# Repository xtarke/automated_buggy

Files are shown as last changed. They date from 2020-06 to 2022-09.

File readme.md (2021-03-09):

# Buggy AWD

Baseado em [Projeto PI3](https://github.com/luscasos/PI3-carro) de __Lucas Odair Silva.__

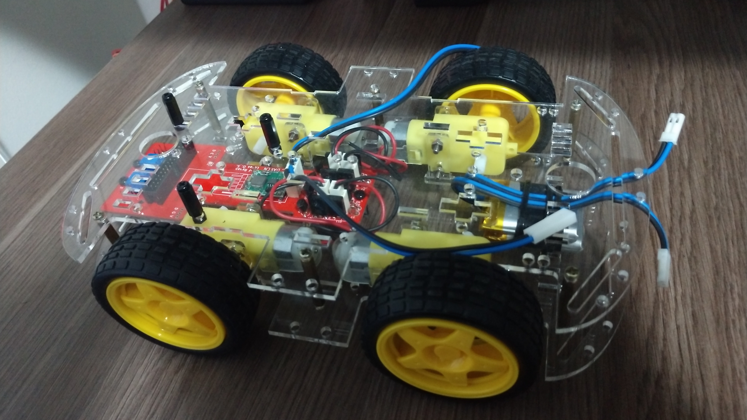
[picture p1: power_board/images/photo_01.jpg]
carro final


## Informações gerais

Projeto da placa eletrônica de potência para o acionamento de um Buggy 4x4. Um conector de 26-vias faz a conexão das seguintes placas:

- [Arduino Uno](./arduino/shield/)
- [MSP-EXP430G2](./msp430/shield_exp430g2)
- [MSP-EXP430FR2355](./msp430/shield_exp430fr2355)
- [Raspberry Pi](./rasp/)

## Características

- Controle independente dos motores (lado esquerdo e lado direito)
- Sensores de velocidade [Encoder](https://www.filipeflop.com/produto/sensor-de-velocidade-encoder/)
- Monitoramento de bateria de LiPo
- Sensor de linha dual
- Sensor ultrassom
- Comunicação Bluetooth (UART)

# Hardware

## Acionamento dos motores

Ponte H

Circuito final de alimentação dos motores, com queda de 0,4V de tensão na carga em relação a VCC e corrente de polarização externa de 640pA, não exigindo muita corrente do microcontrolador.
Ponte H

## Comunicação

HC-05

## Aferição de velocidade

encoder

## Baterias
Para alimentar o carro foram escolhidas duas baterias de LIPO, de 3,7V e 1200mAh, conectadas em série, o que resulta em 7,4V de tensão.

Bateria

## Regulador de tensão
Como o conjunto de baterias tem como tensão 7,4V na saída, é necessário baixar a tensão para níveis aceitáveis para o microcontrolador e modulo bluetooth, no caso foi usado um regulador ajustável Step-up-down, por questão de disponibilidade, mesmo esse sendo superdimensionado para a aplicação em questão, já que suporta correntes de até 5A e nesse caso não passa de 200mA.

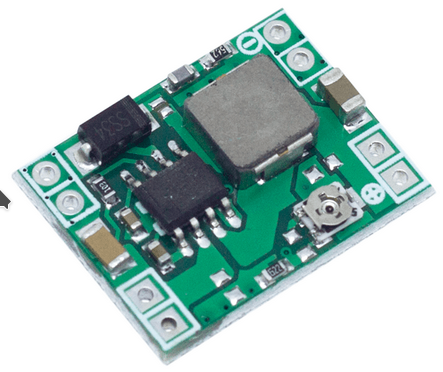
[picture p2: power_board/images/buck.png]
Regulador


## Medição da tensão das baterias
Como regra geral, não se pode descarregar uma bateria abaixo de uma certa tensão, com as usadas nesse projeto não é diferente, não sendo recomendado baixar a tensão da marca dos 3V, como o sistema possui duas baterias é necessário medir a tensão delas individualmente. O conversor analógico digital do microcontrolador tem como tensão base 3V, então é preciso baixar as tensões para menos de 3V, o circuito usado para isso é o diferencial com ampop, que pode dar um ganho menor que 1, sem usar tensão negativa. O Ampop escolhido foi o LM324, com ganho de 1/3 para a tensão superior (bateria 1 em serie com a bateria 2), e de 2/3 para a tensão media (bateria 1).
diferencial

## Placa de circuito

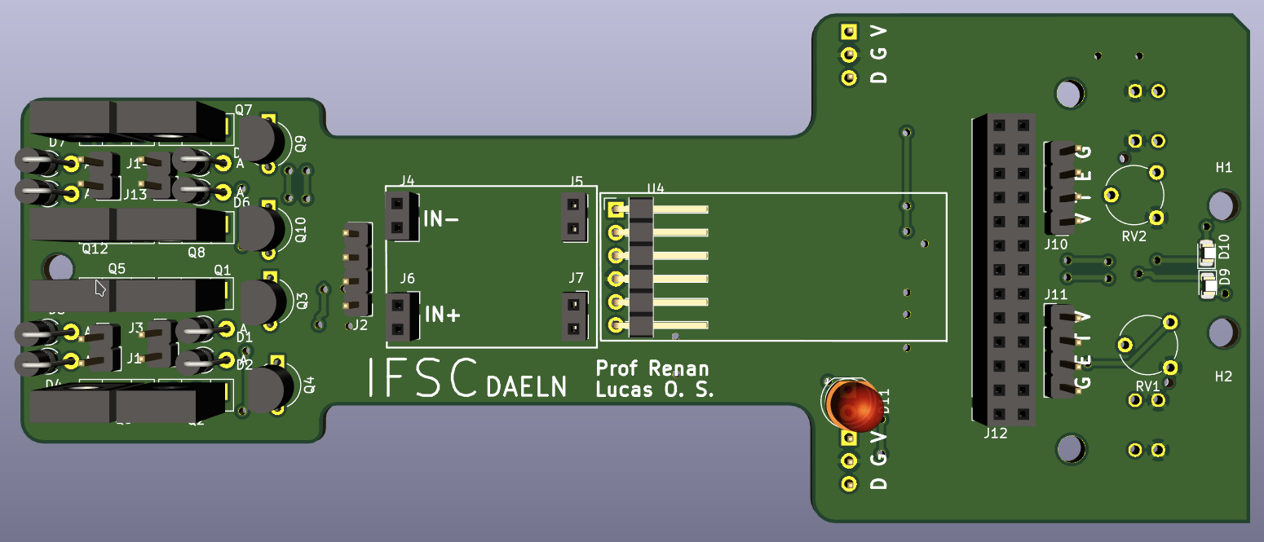
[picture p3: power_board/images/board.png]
carro visto de cima


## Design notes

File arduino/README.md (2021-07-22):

# Interface shield

This shield connects Arduino Uno pins to the car's power board. Go to [Power Board](hhttps://github.com/xtarke/automated_buggy/tree/master/power_board) for more hardware information.

See [this schematic](schematic.pdf).

## Analog pins

| Analog input  | Arduino pin  | Board label  | Signal |
| --- | --- | --- | --- |
| ADC0 | A2 | ADC0 | Bat0 |
| ADC1 | A1 | ADC1 | Bat1 |
| ADC2 | A0 | ADC2 | Ampop1 |
| ADC3 | A3 | ADC3 | Ampop2 |

## Ultrasonic sensor

| Arduino Pin | Signal|
| --- | ---|
| 8 | Echo0 |
| 7 | Trig0 |
| 2 | Echo1 |
| 4 | Trig1 |

## Motors

|Arduino Pin | Signal|  Board label |
| --- | ---| --- |
| 6 | PWM1  |  M1 |
| 5 | PWM1N |  M1N |
| 11 | PWM2  |  M2 |
| 3 | PWM2N |  M2N |

## Speed econder

| Arduino Pin | Signal |  Board label |
| --- | --- | --- |
| 13 | D0 | ENC0 |
| 12 | D1 | ENC1 |

## Optic sensor

| Arduino Pin | Signal | Board label |
| --- | --- | --- |
| A4 | R_TCRT | R DIR |
| A5 | L_TCRT | L ESQ |

## UART

| MSP Pin | Signal |
| --- | --- |
| TX | TX |
| RX | RX |

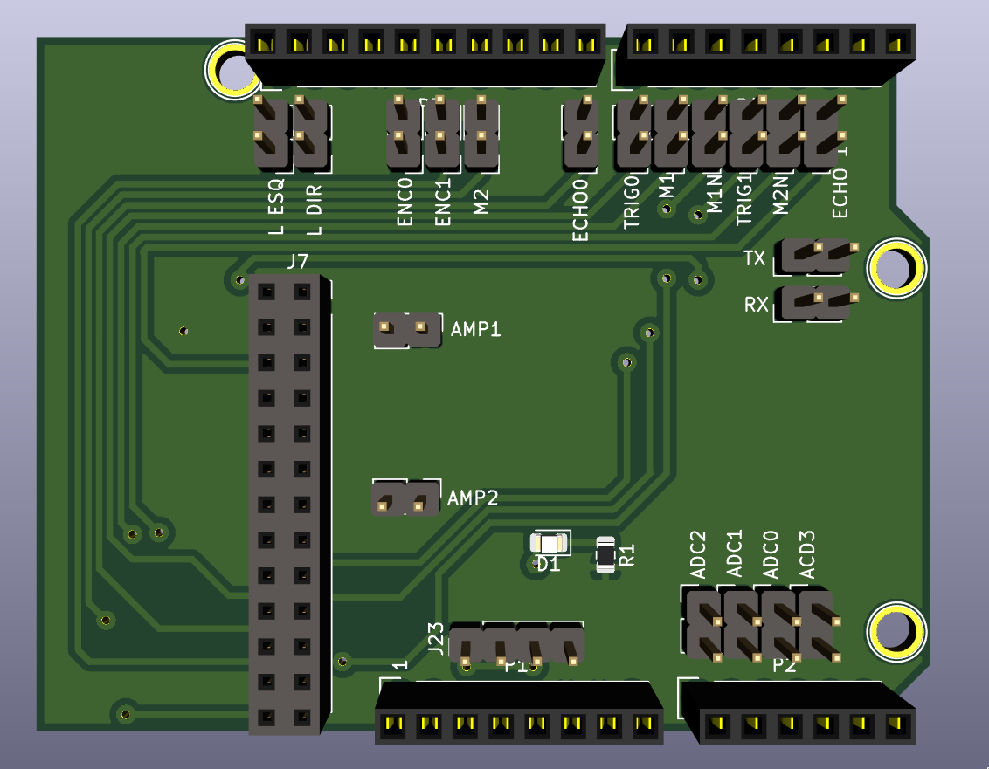
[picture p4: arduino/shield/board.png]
Board


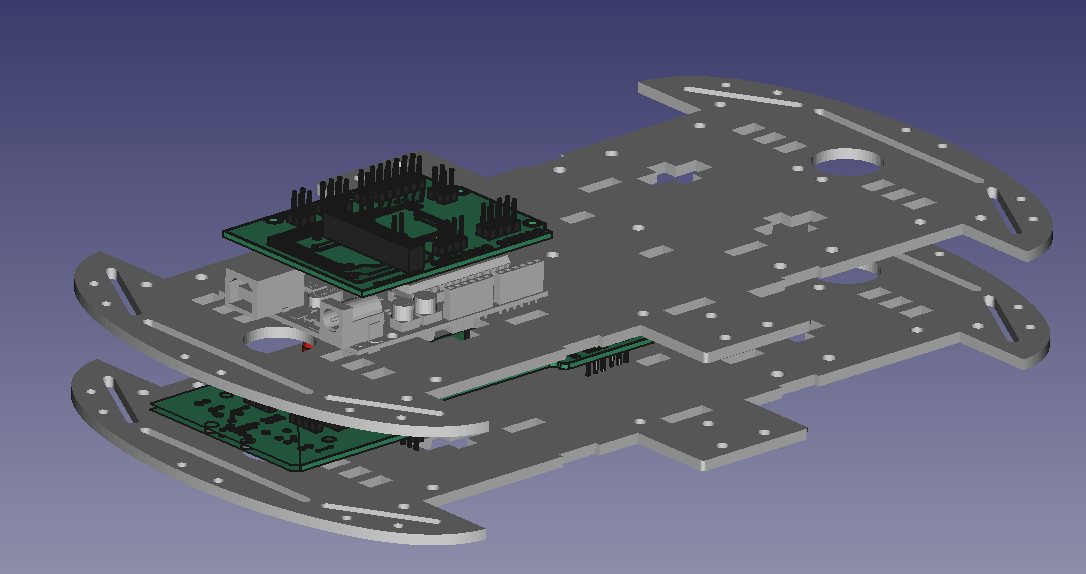
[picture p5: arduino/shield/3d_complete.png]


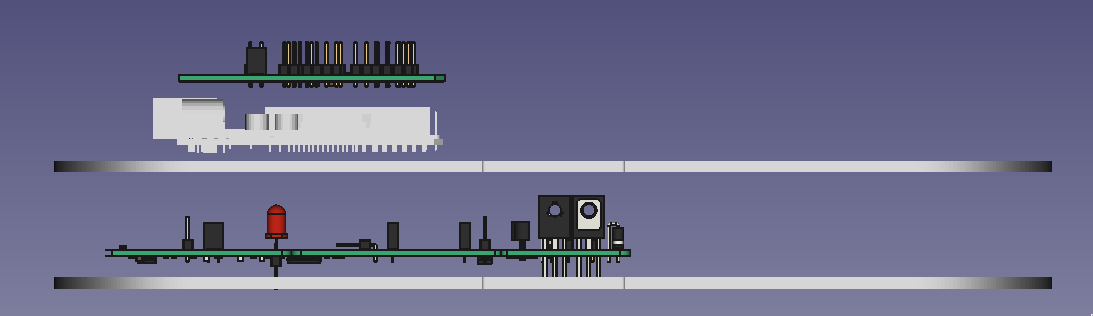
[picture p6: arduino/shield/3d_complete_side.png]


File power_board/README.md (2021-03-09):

# Placa de potência para Buggy AWD

Baseado em [Projeto PI3](https://github.com/luscasos/PI3-carro) de __Lucas Odair Silva.__

carro final

## Informações gerais

Projeto da placa eletrônica de potência para o acionamento de um Buggy 4x4. Um conector de 26-vias faz a conexão das seguintes placas:

- [Arduino Uno](https://github.com/xtarke/avrlibs/tree/master/shields/carrinho_shield)
- [MSP-EXP430G2](https://github.com/xtarke/msplibs/tree/master/hardware/shield_exp430g2)
- [MSP-EXP430FR2355](https://github.com/xtarke/msplibs/tree/master/hardware/shield_exp430fr2355)
- [Raspberry Pi](https://github.com/xtarke/automated_buggy)

## Características

- Controle independente dos motores (lado esquerdo e lado direito)
- Sensores de velocidade [Encoder](https://www.filipeflop.com/produto/sensor-de-velocidade-encoder/)
- Monitoramento de bateria de LiPo
- Sensor de linha dual
- Sensor ultrassom
- Comunicação Bluetooth (UART)

# Hardware

## Acionamento dos motores

Ponte H

Circuito final de alimentação dos motores, com queda de 0,4V de tensão na carga em relação a VCC e corrente de polarização externa de 640pA, não exigindo muita corrente do microcontrolador.
Ponte H

## Comunicação

HC-05

## Aferição de velocidade

encoder

## Baterias
Para alimentar o carro foram escolhidas duas baterias de LIPO, de 3,7V e 1200mAh, conectadas em série, o que resulta em 7,4V de tensão.

Bateria

## Regulador de tensão
Como o conjunto de baterias tem como tensão 7,4V na saída, é necessário baixar a tensão para níveis aceitáveis para o microcontrolador e modulo bluetooth, no caso foi usado um regulador ajustável Step-up-down, por questão de disponibilidade, mesmo esse sendo superdimensionado para a aplicação em questão, já que suporta correntes de até 5A e nesse caso não passa de 200mA.

Regulador

## Medição da tensão das baterias
Como regra geral, não se pode descarregar uma bateria abaixo de uma certa tensão, com as usadas nesse projeto não é diferente, não sendo recomendado baixar a tensão da marca dos 3V, como o sistema possui duas baterias é necessário medir a tensão delas individualmente. O conversor analógico digital do microcontrolador tem como tensão base 3V, então é preciso baixar as tensões para menos de 3V, o circuito usado para isso é o diferencial com ampop, que pode dar um ganho menor que 1, sem usar tensão negativa. O Ampop escolhido foi o LM324, com ganho de 1/3 para a tensão superior (bateria 1 em serie com a bateria 2), e de 2/3 para a tensão media (bateria 1).
diferencial

## Placa de circuito

carro visto de cima

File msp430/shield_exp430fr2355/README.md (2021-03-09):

# Interface shield

This shield connects microcontroller (MSP-EXP430FR2355) pins to the car's power board. Go to [Power Board](https://github.com/xtarke/automated_buggy/tree/master/power_board) for more hardware information.

See [this schematic](schematic.pdf).

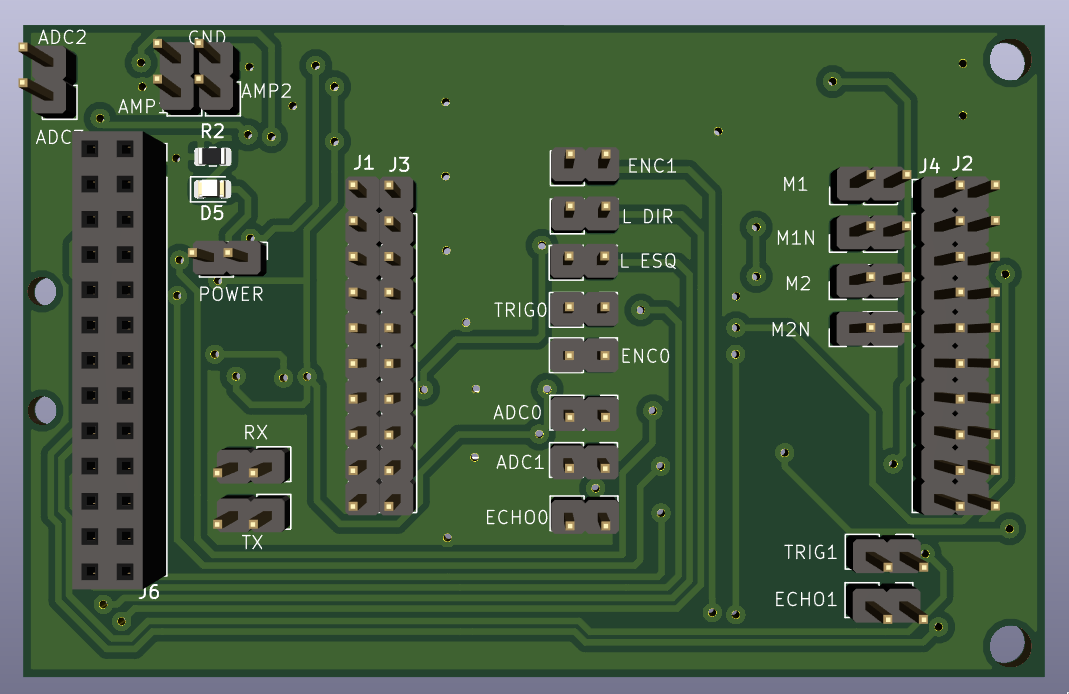
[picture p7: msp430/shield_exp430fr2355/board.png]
Board


## Analog pins

| Analog input  | MSP pin  | Board label  | Signal |
| --- | --- | --- | --- |
| A1 | P1.1 | ADC0 | Bat0 |
| A2 | P1.2 | ADC1 | Bat1 |
| ? |  ? | ADC2 | Ampop1 |
| ? |  ? | ADC3 | Ampop2 |

## Ultrasonic sensor

| MSP Pin | Signal|
| --- | ---|
| P2.0/TB1.1  | Echo0 |
| P2.2 | Trig0 |
| P2.1/TB1.2  | Echo1 |
| P2.4 | Trig1 |

## Motors

| MSP Pin | Signal|  Board label |
| --- | ---| --- |
| P6.0/TB3.1 | PWM1  |  M1 |
| P6.1/TB3.2 | PWM1N |  M1N |
| P6.2/TB3.3 | PWM2  |  M2 |
| P6.3/TB3.4 | PWM2N |  M2N |

## Espeed econder

| MSP Pin | Signal |  Board label |
| --- | --- | --- |
| P5.0 | D0 | ENC0 |
| P5.1 | D1 | ENC1 |

## Optic sensor

| MSP Pin | Signal | Board label |
| --- | --- | --- |
| P5.4 | R_TCRT | R DIR |
| P3.0 | L_TCRT | L ESQ |

## UART

| MSP Pin | Signal |
| --- | --- |
| P1.7 | TX |
| P1.6 | RX |

## Assembly

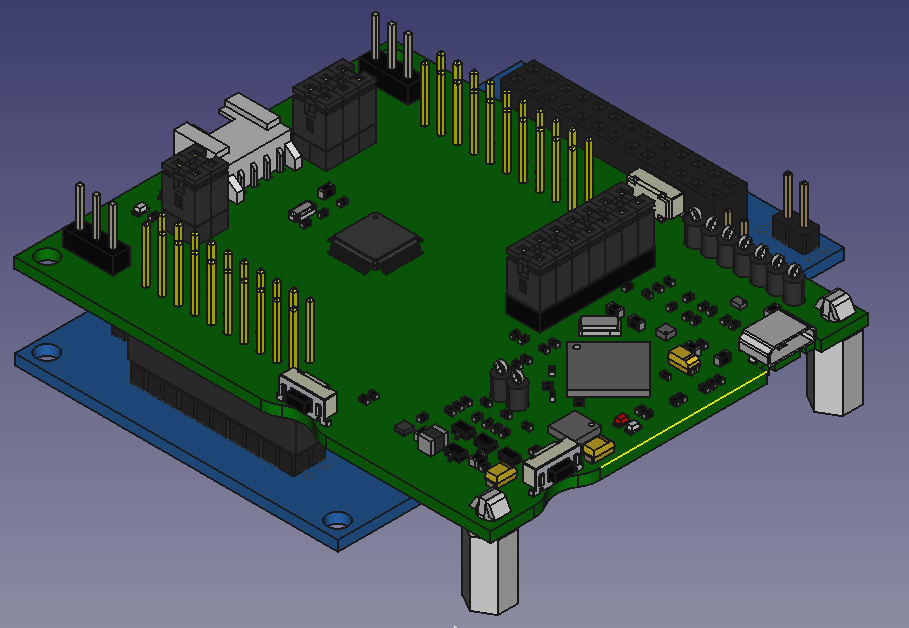
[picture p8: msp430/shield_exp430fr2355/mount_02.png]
Shield Board
Shield and EXP430FR2355 

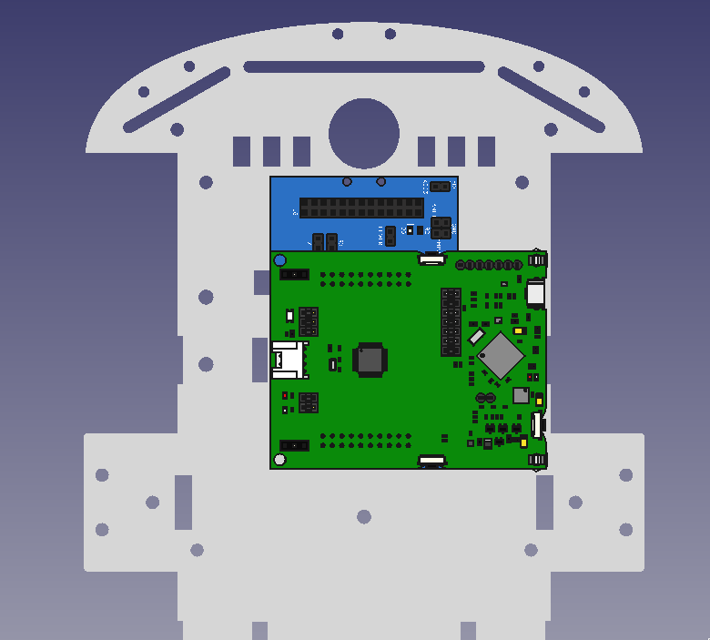
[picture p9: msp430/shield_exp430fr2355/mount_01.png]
Shield Board
Shield, EXP430FR2355 and chassi. 

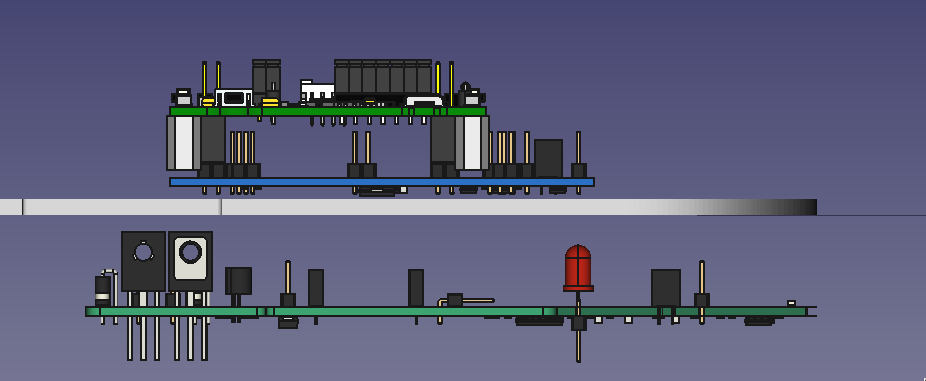
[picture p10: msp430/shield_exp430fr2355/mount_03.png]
Shield Board
Power board. Connection with 26 pin flat cable

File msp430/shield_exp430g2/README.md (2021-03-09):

# Interface shield

This shield connects all microcontroller (MSP-EXP430G2 - MSP430G2553) pins to the car's power board. Go to [Power Board](https://github.com/xtarke/automated_buggy/tree/master/power_board) for more hardware information.

See [this schematic](schematic.pdf).

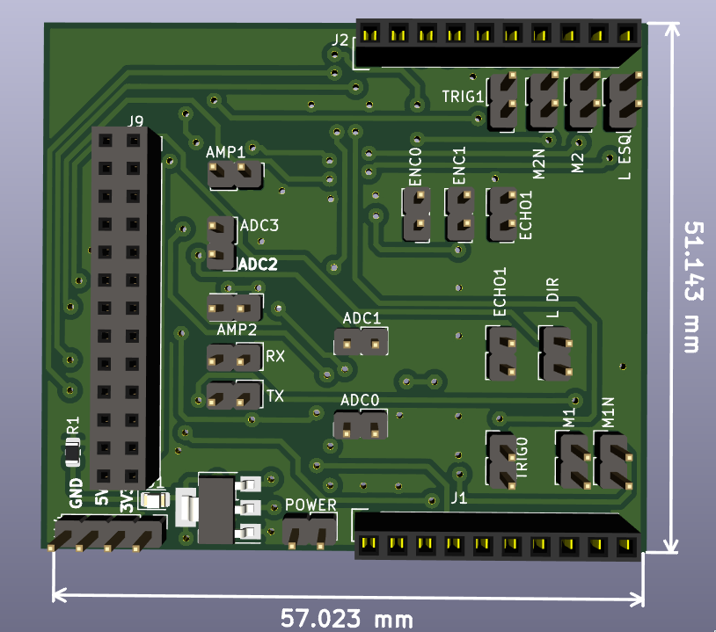
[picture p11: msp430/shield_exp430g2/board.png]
Shield Board


## Analog pins

| Analog input  | MSP pin  | Board label  | Signal |
| --- | --- | --- | --- |
| A0 | P1.0 | ADC0 | Bat0 |
| A3 | P1.3 | ADC1 | Bat1 |
| ? |  ? | ADC2 | Ampop1 |
| ? |  ? | ADC3 | Ampop2 |

## Ultrasonic sensor

| MSP Pin | Signal|
| --- | ---|
| P1.5 | Echo0 |
| P1.4 | Trig0 |
| P1.6 | Echo1 |
| P1.7 | Trig1 |

## Motors

**Caution**, P2.1 and P2.2 are connected to the same timer comparator as well as P2.4 and P2.5.

| MSP Pin | Signal|  Board label |
| --- | ---| --- |
| P2.1/TA1.1 | PWM1  |  M1 |
| P2.2/TA1.1 | PWM1N |  M1N |
| P2.4/TA1.2 | PWM2  |  M2 |
| P2.5/TA1.2 | PWM2N |  M2N |

## Espeed econder

| MSP Pin | Signal |  Board label |
| --- | --- | --- |
| P2.6 | D0 | ENC0 |
| P2.7 | D1 | ENC1 |

## Optic sensor

| MSP Pin | Signal | Board label |
| --- | --- | --- |
| P2.0 | R_TCRT | R DIR |
| P2.3 | L_TCRT | L ESQ |

## UART

| MSP Pin | Signal |
| --- | --- |
| P1.2 | TX |
| P1.3 | RX |

## Assembly

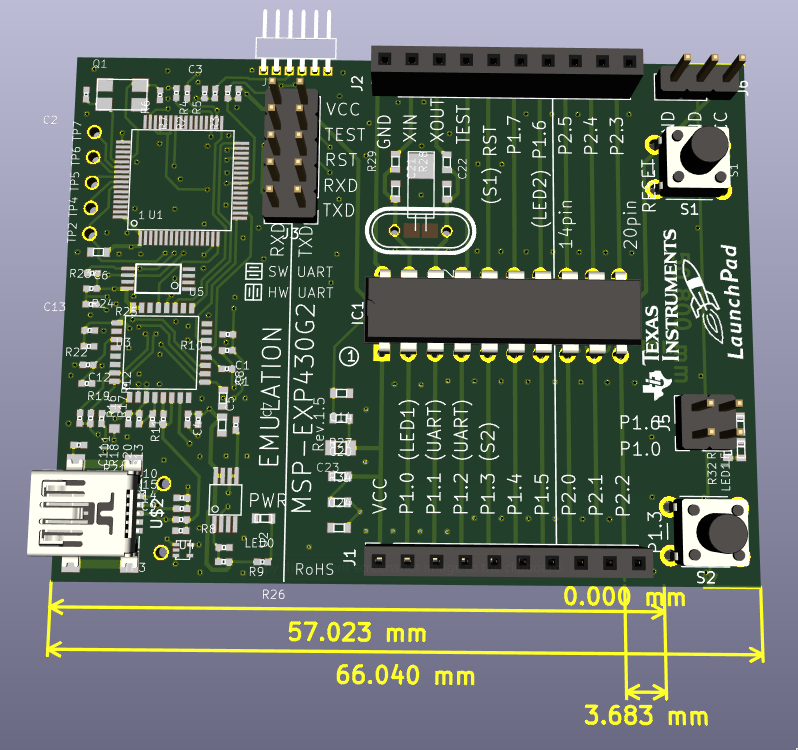
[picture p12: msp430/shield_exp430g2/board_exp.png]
Shield Board
EXP430G2 with MSP430G2553 
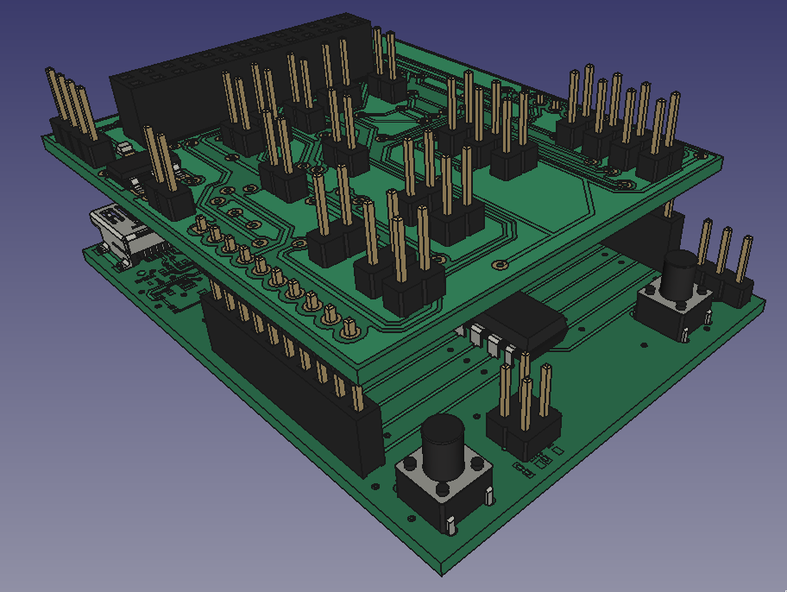
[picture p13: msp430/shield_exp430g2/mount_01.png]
Shield Board
Shield and EXP430G2 
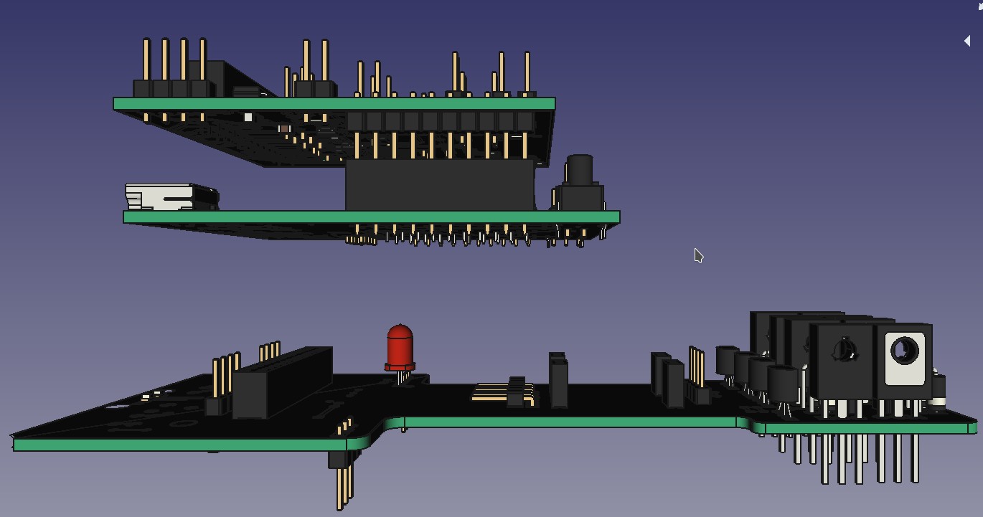
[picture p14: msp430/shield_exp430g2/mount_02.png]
Shield Board
Power board. Connection with 26 pin flat cable

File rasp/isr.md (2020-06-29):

https://raspi.tv/2013/how-to-use-interrupts-with-python-on-the-raspberry-pi-and-rpi-gpio-part-3

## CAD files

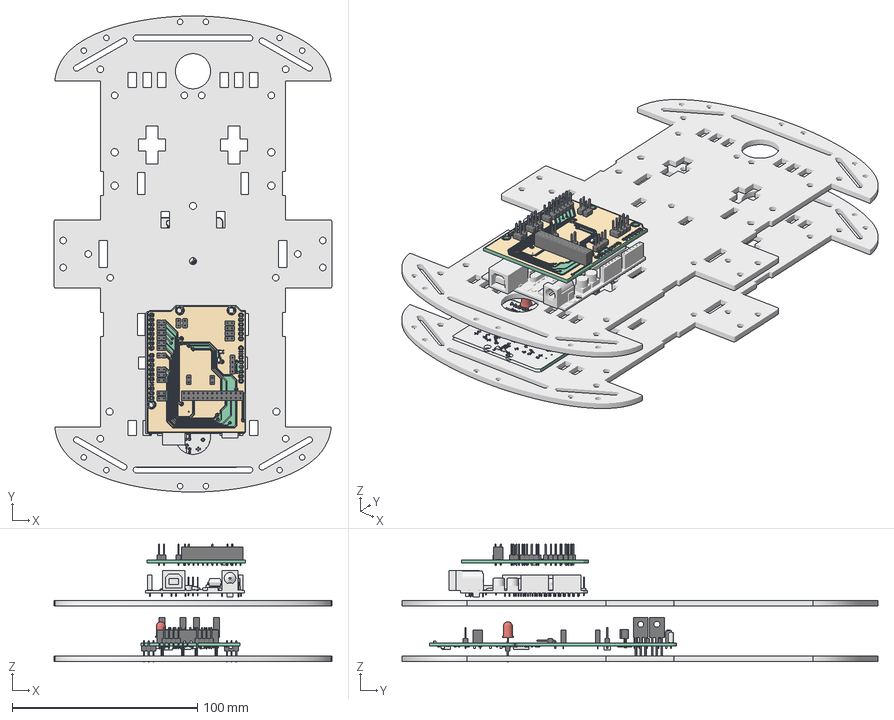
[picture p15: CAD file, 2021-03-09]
arduino/shield/3d/3dmodel.FCStd
150.0 x 257.0 x 63.7 mm
Pcb_504c
topTracks_504c
botTracks_504c
D10_LED_0805_2012Metric_5D8FAA55
D9_LED_0805_2012Metric_5D8F5CB8
Q10_TO-92_Inline_Wide_5D144232
Q4_TO-92_Inline_Wide_5D14421F
Q9_TO-92_Inline_Wide_5D14420C
Q3_TO-92_Inline_Wide_5D1441F9
J10_PinHeader_1x04_P254mm_Vertical_5CCA68DD
U4_PinHeader_1x06_P254mm_Horizontal_5D1180CB
J11_PinHeader_1x04_P254mm_Vertical_5CCA68C5
J5_PinSocket_1x02_P254mm_Vertical_5CEE14AB
J12_PinSocket_2x13_P254mm_Vertical_5CEE7202
J6_PinSocket_1x02_P254mm_Vertical_5CEE1496
J7_PinSocket_1x02_P254mm_Vertical_5CEE1481
J4_PinSocket_1x02_P254mm_Vertical_5CEE14C0
Q12_TO-126-3_Vertical_5CBBB90E
Q6_TO-126-3_Vertical_5CB9F0CD
Q8_TO-126-3_Vertical_5CB9F14F
D6_D_A-405_P2.54mm_Vertical_AnodeUp_5CC2F82E
D7_D_A-405_P2.54mm_Vertical_AnodeUp_5CC2FCEA
D2_D_A-405_P2.54mm_Vertical_AnodeUp_5CC2F84C
D3_D_A-405_P2.54mm_Vertical_AnodeUp_5D89E26B
D8_D_A-405_P2.54mm_Vertical_AnodeUp_5D84EFBF
D4_D_A-405_P2.54mm_Vertical_AnodeUp_5CC2F86A
Q1_TO-126-3_Vertical_5CBBB9BD
Q2_TO-126-3_Vertical_5CBBB9A4
Q11_TO-126-3_Vertical_5CBBB927
Q7_TO-126-3_Vertical_5CB9F135
Q5_TO-126-3_Vertical_5CB9F0E7
D1_D_A-405_P2.54mm_Vertical_AnodeUp_5CC2F85B
D5_D_A-405_P2.54mm_Vertical_AnodeUp_5CC2F800
J2_PinHeader_1x04_P254mm_Vertical_5D8375DE
J13_PinHeader_1x02_P254mm_Vertical_5D84BA2C
J14_PinHeader_1x02_P254mm_Vertical_5D84CC03
J1_PinHeader_1x02_P254mm_Vertical_5D84C8B4
J3_PinHeader_1x02_P254mm_Vertical_5D84C8C9
D11_LED_D5.0mm_5DC05149
C3_C_0805_2012Metric_5D605FC9
D12_D_SMB_5D89B82C
R35_R_0805_2012Metric_5D8A9567
U3_SOIC_14_39x87mm_P127mm_5D51740A
R34_R_0805_2012Metric_5D4B9DB6
R33_R_0805_2012Metric_5D4B9DA5
J8_PinHeader_1x03_P254mm_Vertical_5CC7F0D8
R26_R_0805_2012Metric_5D1A85D7
R25_R_0805_2012Metric_5CD50FA7
R28_R_0805_2012Metric_5CD50FDA
R31_R_0805_2012Metric_5D143DC4
C2_C_0805_2012Metric_5D1448C2
C1_C_0805_2012Metric_5D1448B1
R32_R_0805_2012Metric_5D143DB3
R12_R_0805_2012Metric_5CC39C34
R13_R_0805_2012Metric_5CC39C24
R14_R_0805_2012Metric_5CC39C14
R18_R_0805_2012Metric_5CD46DAC
R19_R_0805_2012Metric_5CD46D9B
R15_R_0805_2012Metric_5CC39C04
U1_SOIC_8_39x49mm_P127mm_5CD4E5C4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

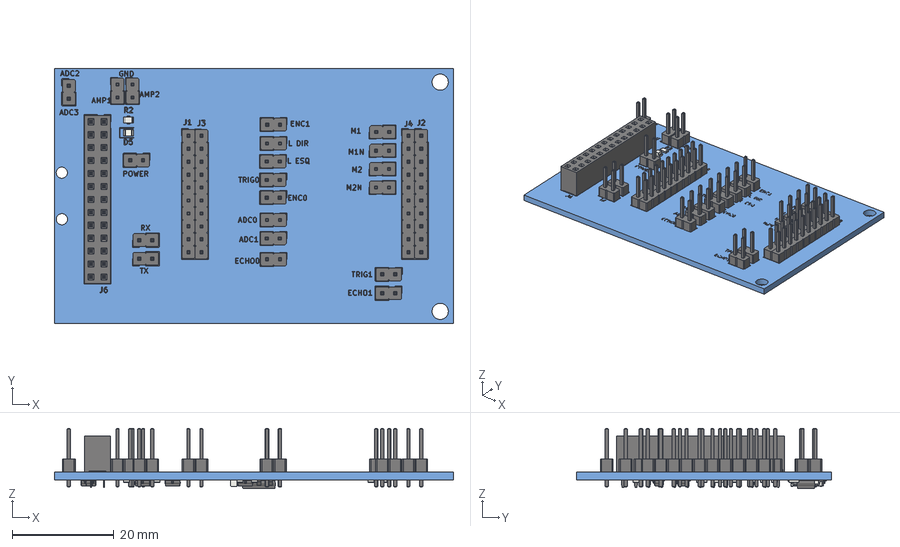
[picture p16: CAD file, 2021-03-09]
msp430/shield_exp430fr2355/3d/shield.FCStd
78.4 x 50.0 x 11.8 mm
Pcb_6e80
topSilks_5e37
J4_PinHeader_1x10_P254mm_Vertical_5EF7C818
J2_PinHeader_1x10_P254mm_Vertical_5EF7DC5C
J19_PinHeader_1x02_P254mm_Vertical_5EF86645
J28_PinHeader_1x02_P254mm_Vertical_5EF8662F
J27_PinHeader_1x02_P254mm_Vertical_5EF86619
J25_PinHeader_1x02_P254mm_Vertical_5EF88DF8
J23_PinHeader_1x02_P254mm_Vertical_5EFAA149
J7_PinHeader_1x02_P254mm_Vertical_5EF865D7
J8_PinHeader_1x02_P254mm_Vertical_5EF865C1
J9_PinHeader_1x02_P254mm_Vertical_5EF865AB
J10_PinHeader_1x02_P254mm_Vertical_5EF86595
J12_PinHeader_1x02_P254mm_Vertical_5EF8E749
J13_PinHeader_1x02_P254mm_Vertical_5EF86569
J15_PinHeader_1x02_P254mm_Vertical_5EF86553
J16_PinHeader_1x02_P254mm_Vertical_5EF9213C
J17_PinHeader_1x02_P254mm_Vertical_5EF86527
J18_PinHeader_1x02_P254mm_Vertical_5EF919EE
J20_PinHeader_1x02_P254mm_Vertical_5EF864FB
J21_PinHeader_1x02_P254mm_Vertical_5EF864E5
J22_PinHeader_1x02_P254mm_Vertical_5EF864CF
J24_PinHeader_1x02_P254mm_Vertical_5EF864B9
J14_PinHeader_1x02_P254mm_Vertical_5EF864A3
J3_PinHeader_1x10_P254mm_Vertical_5EF7D2E3
J6_PinSocket_2x13_P254mm_Vertical_5EF552A6
D5_LED_0805_2012Metric_5EF17365
R2_R_0805_2012Metric_5EF53075
J1_PinHeader_1x10_P254mm_Vertical_5EF7B795
C2_C_0805_2012Metric_5EF37C61
C1_C_0805_2012Metric_5EF17607
U1_SOT_223_5EF17352
Q1_SOT_23_5EF1733C
D1_SOT_23_5EF17327
D2_SOT_23_5EF17312
D3_SOT_23_5EF51381
D4_SOT_23_5EF172E8
Q2_SOT_23_5EF497E2
R12_R_0805_2012Metric_5EF46901
R11_R_0805_2012Metric_5EF172AD
R10_R_0805_2012Metric_5EF1729C
R9_R_0805_2012Metric_5EF640D5
R8_R_0805_2012Metric_5EF1727A
R7_R_0805_2012Metric_5EF17269
R6_R_0805_2012Metric_5EF17258
R13_R_0805_2012Metric_5EF3A85A
R14_R_0805_2012Metric_5EF37FD2
R15_R_0805_2012Metric_5EF3AB4A
R4_R_0805_2012Metric_5EF17214
R3_R_0805_2012Metric_5EF17203
R1_R_0805_2012Metric_5EF59A96
R5_R_0805_2012Metric_5EF171E1

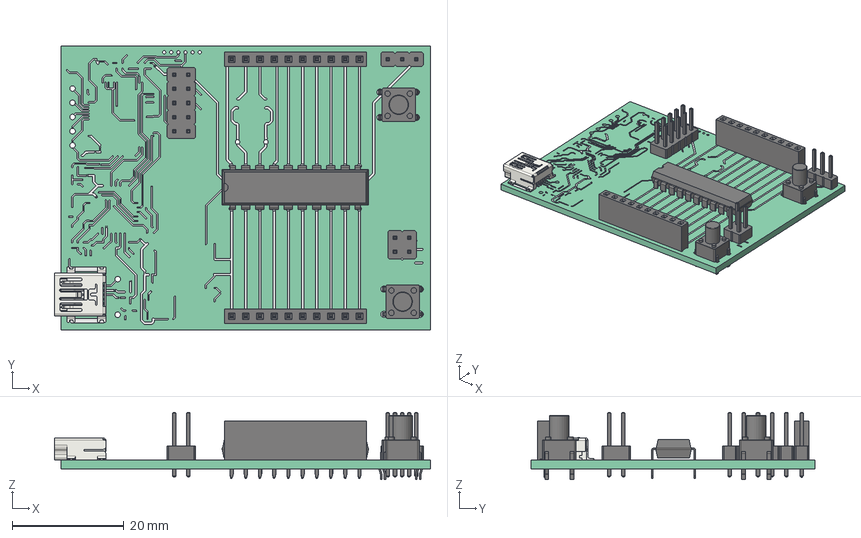
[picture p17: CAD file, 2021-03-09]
msp430/shield_exp430g2/3d/exp430g2.FCStd
67.2 x 50.8 x 12.0 mm
Pcb_a96f
topTracks_a96f
botTracks_a96f
S2_SW_PUSH_6mm_h8mm_5EF632D4
S1_SW_PUSH_6mm_h8mm_5EF632BE
U$2_USB_Mini-B_Lumberg_2486_01_Horizontal_5EF63352
J3_PinHeader_2x05_P254mm_Vertical_5EF648FA
J5_PinHeader_2x02_P254mm_Vertical_5EF648CB
J6_PinHeader_1x03_P254mm_Vertical_5EF630EB
J2_PinSocket_1x10_P254mm_Vertical_5EF6310A
J1_PinSocket_1x10_P254mm_Vertical_5EF631DF
IC1_DIP-20_W7.62mm_5EF6336D

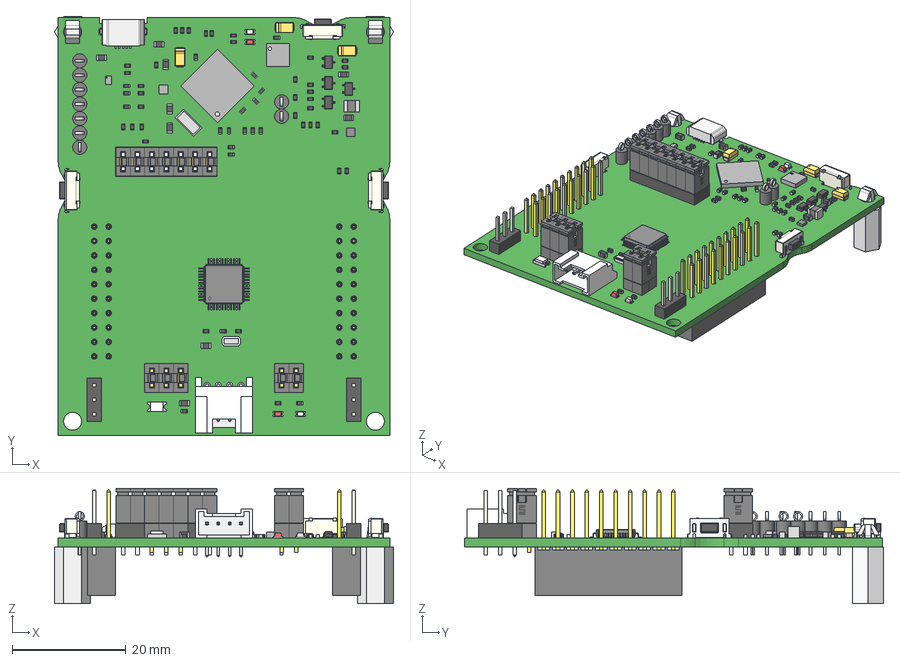
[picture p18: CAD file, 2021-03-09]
msp430/shield_exp430fr2355/3d/exp-msp430fr2355.step
59.7 x 73.9 x 20.3 mm
SamtecTSWpin x 10
SamtecTSWbody x 10
MAE-10 x 2
Extruded x 241
1188E-1K2-V-TR_1 x 3
1188E-1K2-V-TR_2 x 3
1188E-1K2-V-TR_3 x 3
1188E-1K2-V-TR_4 x 3
1188E-1K2-V-TR_5 x 3
1188E-1K2-V-TR_6 x 3
1188E-1K2-V-TR_7 x 3
PT0048A_1
PT0048A_2 x 48
Lite-On_LTST_C190 x 2
Lite-On_LTST_C190_red x 2
SSQ-110-03-T-D_2 x 2
SSQ-110-03-T-D_1 x 2
Case_Anode_2 x 3
Case_Bottom_2 x 3
Case_Cathode_2 x 3
Case_Top_2_2 x 3
User_Library-SC-70_pin_TSSOP_tssop6_1 x 12
User_Library-SC-70_body_TSSOP-6_SC70_1 x 4
FRAME-RSE0008A_3
FRAME-RSE0008A_4
FRAME-RSE0008A_5
FRAME-RSE0008A_6
FRAME-RSE0008A_7
FRAME-RSE0008A_8
FRAME-RSE0008A_9
FRAME-RSE0008A_10
BODY-QFN
PIN1-ID
Keystone5001_black x 9
Keystone500x_wire x 9
c-37-x x 12
snt-100-xx x 12

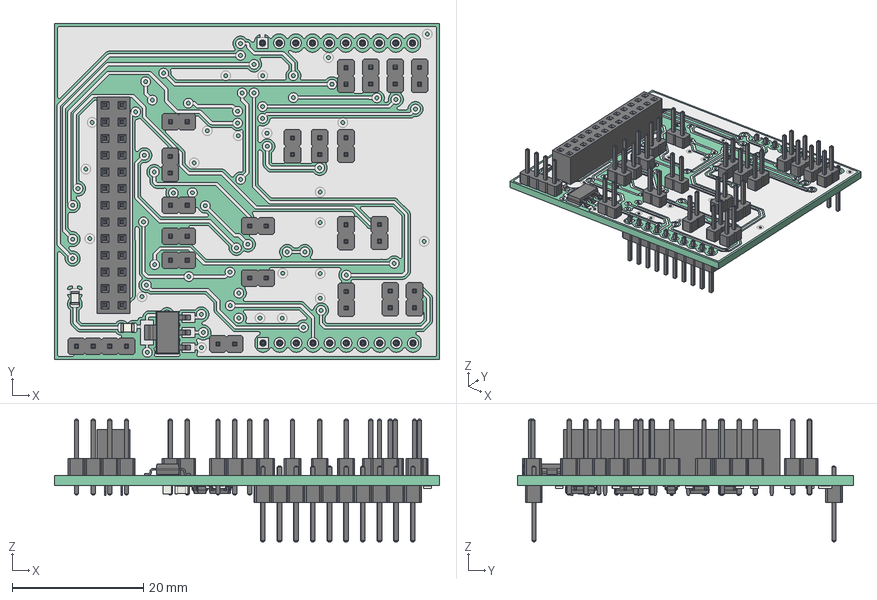
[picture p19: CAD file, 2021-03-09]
msp430/shield_exp430g2/3d/shield.FCStd
58.7 x 51.2 x 18.7 mm
Pcb_48dc
topTracks_48dc
botTracks_48dc
POWER_PinHeader_1x02_P254mm_Vertical_5EE1416E
J9_PinSocket_2x13_P254mm_Vertical_5EE14100
U1_SOT_223_5EEEE608
ADC1_PinHeader_1x02_P254mm_Vertical_5EE15095
ADC0_PinHeader_1x02_P254mm_Vertical_5EECB025
ENC1_PinHeader_1x02_P254mm_Vertical_5EE142CE
RX_PinHeader_1x02_P254mm_Vertical_5EE142B8
TX_PinHeader_1x02_P254mm_Vertical_5EE142A2
ENC0_PinHeader_1x02_P254mm_Vertical_5EEE9EC4
"L ESQ"_PinHeader_1x02_P254mm_Vertical_5EEE0732
ECHO1_PinHeader_1x02_P254mm_Vertical_5EED78E7
"L DIR"_PinHeader_1x02_P254mm_Vertical_5EED064D
M2N_PinHeader_1x02_P254mm_Vertical_5EED1EB6
M1N_PinHeader_1x02_P254mm_Vertical_5EED05A3
M1_PinHeader_1x02_P254mm_Vertical_5EED018C
TRIG1_PinHeader_1x02_P254mm_Vertical_5EE141F2
TRIG0_PinHeader_1x02_P254mm_Vertical_5EE141DC
ECHO1_PinHeader_1x02_P254mm_Vertical_5EE141C6
ADC3_PinHeader_1x02_P254mm_Vertical_5EED8CB7
AMP2_PinHeader_1x02_P254mm_Vertical_5EE1419A
AMP1_PinHeader_1x02_P254mm_Vertical_5EEBCC45
M2_PinHeader_1x02_P254mm_Vertical_5EE1412E
J14_PinHeader_1x04_P254mm_Vertical_5EE14118
D1_LED_0805_2012Metric_5EED593B
R1_R_0805_2012Metric_5EF1D82C
J2_PinHeader_1x10_P254mm_Vertical_5EE16093
J1_PinHeader_1x10_P254mm_Vertical_5EF1B141
Q1_SOT_23_5EE3ECDD
Q2_SOT_23_5EEDBF09
D2_SOT_23_5EE3ECB3
D3_SOT_23_5EE3EC9E
D4_SOT_23_5EF1C4D7
D5_SOT_23_5EEDA13F
R12_R_0805_2012Metric_5EE3EC5F
R4_R_0805_2012Metric_5EED870F
R5_R_0805_2012Metric_5EED8C6C
R2_R_0805_2012Metric_5EE3EC2C
R6_R_0805_2012Metric_5EE3EC1B
R7_R_0805_2012Metric_5EE3EC0A
R8_R_0805_2012Metric_5EECED37
R9_R_0805_2012Metric_5EF16275
R10_R_0805_2012Metric_5EEEA797
R11_R_0805_2012Metric_5EE3EBA6
R13_R_0805_2012Metric_5EECFE3A
R14_R_0805_2012Metric_5EE3EB84
R15_R_0805_2012Metric_5EEDB8CD
R3_R_0805_2012Metric_5EE3EB62
C2_C_0805_2012Metric_5EEEEF76
C1_C_0805_2012Metric_5EE142DF

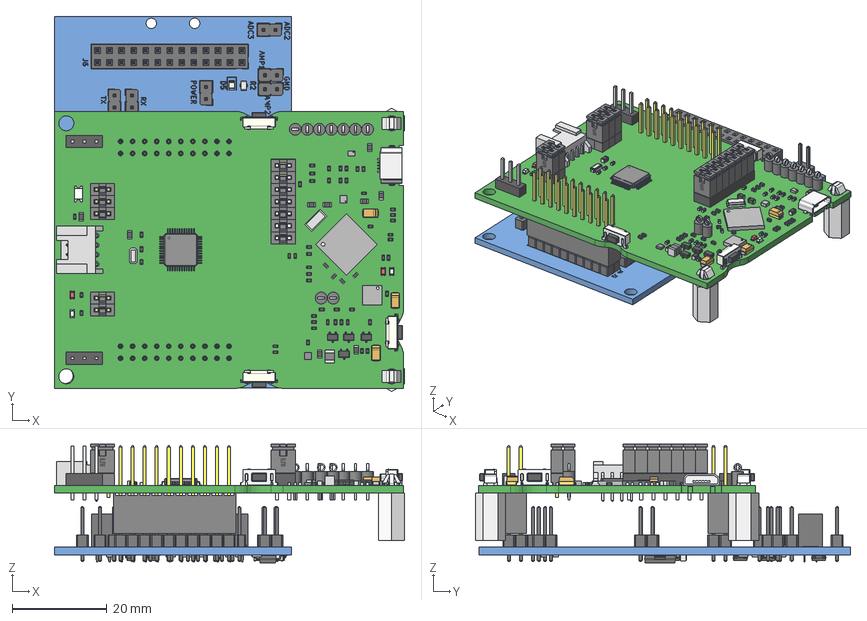
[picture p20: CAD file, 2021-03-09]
msp430/shield_exp430fr2355/3d/mount_fr.FCStd
73.9 x 79.0 x 25.0 mm
Pcb_6e80
topSilks_5e37
J4_PinHeader_1x10_P254mm_Vertical_5EF7C818
J2_PinHeader_1x10_P254mm_Vertical_5EF7DC5C
J19_PinHeader_1x02_P254mm_Vertical_5EF86645
J28_PinHeader_1x02_P254mm_Vertical_5EF8662F
J27_PinHeader_1x02_P254mm_Vertical_5EF86619
J25_PinHeader_1x02_P254mm_Vertical_5EF88DF8
J23_PinHeader_1x02_P254mm_Vertical_5EFAA149
J7_PinHeader_1x02_P254mm_Vertical_5EF865D7
J8_PinHeader_1x02_P254mm_Vertical_5EF865C1
J9_PinHeader_1x02_P254mm_Vertical_5EF865AB
J10_PinHeader_1x02_P254mm_Vertical_5EF86595
J12_PinHeader_1x02_P254mm_Vertical_5EF8E749
J13_PinHeader_1x02_P254mm_Vertical_5EF86569
J15_PinHeader_1x02_P254mm_Vertical_5EF86553
J16_PinHeader_1x02_P254mm_Vertical_5EF9213C
J17_PinHeader_1x02_P254mm_Vertical_5EF86527
J18_PinHeader_1x02_P254mm_Vertical_5EF919EE
J20_PinHeader_1x02_P254mm_Vertical_5EF864FB
J21_PinHeader_1x02_P254mm_Vertical_5EF864E5
J22_PinHeader_1x02_P254mm_Vertical_5EF864CF
J24_PinHeader_1x02_P254mm_Vertical_5EF864B9
J14_PinHeader_1x02_P254mm_Vertical_5EF864A3
J3_PinHeader_1x10_P254mm_Vertical_5EF7D2E3
J6_PinSocket_2x13_P254mm_Vertical_5EF552A6
D5_LED_0805_2012Metric_5EF17365
R2_R_0805_2012Metric_5EF53075
J1_PinHeader_1x10_P254mm_Vertical_5EF7B795
C2_C_0805_2012Metric_5EF37C61
C1_C_0805_2012Metric_5EF17607
U1_SOT_223_5EF17352
Q1_SOT_23_5EF1733C
D1_SOT_23_5EF17327
D2_SOT_23_5EF17312
D3_SOT_23_5EF51381
D4_SOT_23_5EF172E8
Q2_SOT_23_5EF497E2
R12_R_0805_2012Metric_5EF46901
R11_R_0805_2012Metric_5EF172AD
R10_R_0805_2012Metric_5EF1729C
R9_R_0805_2012Metric_5EF640D5
R8_R_0805_2012Metric_5EF1727A
R7_R_0805_2012Metric_5EF17269
R6_R_0805_2012Metric_5EF17258
R13_R_0805_2012Metric_5EF3A85A
R14_R_0805_2012Metric_5EF37FD2
R15_R_0805_2012Metric_5EF3AB4A
R4_R_0805_2012Metric_5EF17214
R3_R_0805_2012Metric_5EF17203
R1_R_0805_2012Metric_5EF59A96
R5_R_0805_2012Metric_5EF171E1
SamtecTSWpin
SamtecTSWbody
SamtecTSWbody001
SamtecTSWpin001
SamtecTSWpin002
SamtecTSWbody002
SamtecTSWbody003
SamtecTSWpin003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

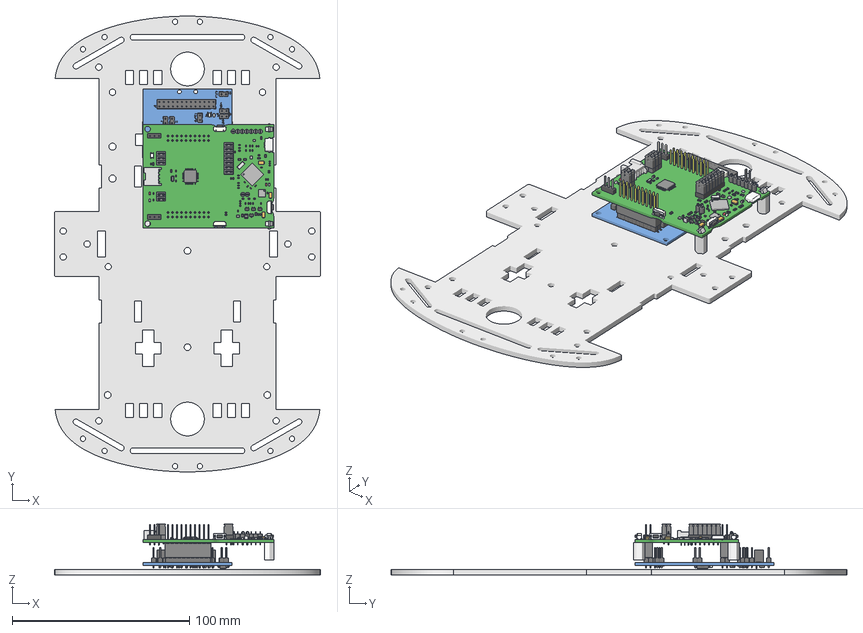
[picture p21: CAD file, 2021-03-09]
msp430/shield_exp430fr2355/3d/mount.FCStd
150.0 x 257.0 x 28.7 mm
Pcb_6e80
topSilks_5e37
J4_PinHeader_1x10_P254mm_Vertical_5EF7C818
J2_PinHeader_1x10_P254mm_Vertical_5EF7DC5C
J19_PinHeader_1x02_P254mm_Vertical_5EF86645
J28_PinHeader_1x02_P254mm_Vertical_5EF8662F
J27_PinHeader_1x02_P254mm_Vertical_5EF86619
J25_PinHeader_1x02_P254mm_Vertical_5EF88DF8
J23_PinHeader_1x02_P254mm_Vertical_5EFAA149
J7_PinHeader_1x02_P254mm_Vertical_5EF865D7
J8_PinHeader_1x02_P254mm_Vertical_5EF865C1
J9_PinHeader_1x02_P254mm_Vertical_5EF865AB
J10_PinHeader_1x02_P254mm_Vertical_5EF86595
J12_PinHeader_1x02_P254mm_Vertical_5EF8E749
J13_PinHeader_1x02_P254mm_Vertical_5EF86569
J15_PinHeader_1x02_P254mm_Vertical_5EF86553
J16_PinHeader_1x02_P254mm_Vertical_5EF9213C
J17_PinHeader_1x02_P254mm_Vertical_5EF86527
J18_PinHeader_1x02_P254mm_Vertical_5EF919EE
J20_PinHeader_1x02_P254mm_Vertical_5EF864FB
J21_PinHeader_1x02_P254mm_Vertical_5EF864E5
J22_PinHeader_1x02_P254mm_Vertical_5EF864CF
J24_PinHeader_1x02_P254mm_Vertical_5EF864B9
J14_PinHeader_1x02_P254mm_Vertical_5EF864A3
J3_PinHeader_1x10_P254mm_Vertical_5EF7D2E3
J6_PinSocket_2x13_P254mm_Vertical_5EF552A6
D5_LED_0805_2012Metric_5EF17365
R2_R_0805_2012Metric_5EF53075
J1_PinHeader_1x10_P254mm_Vertical_5EF7B795
C2_C_0805_2012Metric_5EF37C61
C1_C_0805_2012Metric_5EF17607
U1_SOT_223_5EF17352
Q1_SOT_23_5EF1733C
D1_SOT_23_5EF17327
D2_SOT_23_5EF17312
D3_SOT_23_5EF51381
D4_SOT_23_5EF172E8
Q2_SOT_23_5EF497E2
R12_R_0805_2012Metric_5EF46901
R11_R_0805_2012Metric_5EF172AD
R10_R_0805_2012Metric_5EF1729C
R9_R_0805_2012Metric_5EF640D5
R8_R_0805_2012Metric_5EF1727A
R7_R_0805_2012Metric_5EF17269
R6_R_0805_2012Metric_5EF17258
R13_R_0805_2012Metric_5EF3A85A
R14_R_0805_2012Metric_5EF37FD2
R15_R_0805_2012Metric_5EF3AB4A
R4_R_0805_2012Metric_5EF17214
R3_R_0805_2012Metric_5EF17203
R1_R_0805_2012Metric_5EF59A96
R5_R_0805_2012Metric_5EF171E1
SamtecTSWpin
SamtecTSWbody
SamtecTSWbody001
SamtecTSWpin001
SamtecTSWpin002
SamtecTSWbody002
SamtecTSWbody003
SamtecTSWpin003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

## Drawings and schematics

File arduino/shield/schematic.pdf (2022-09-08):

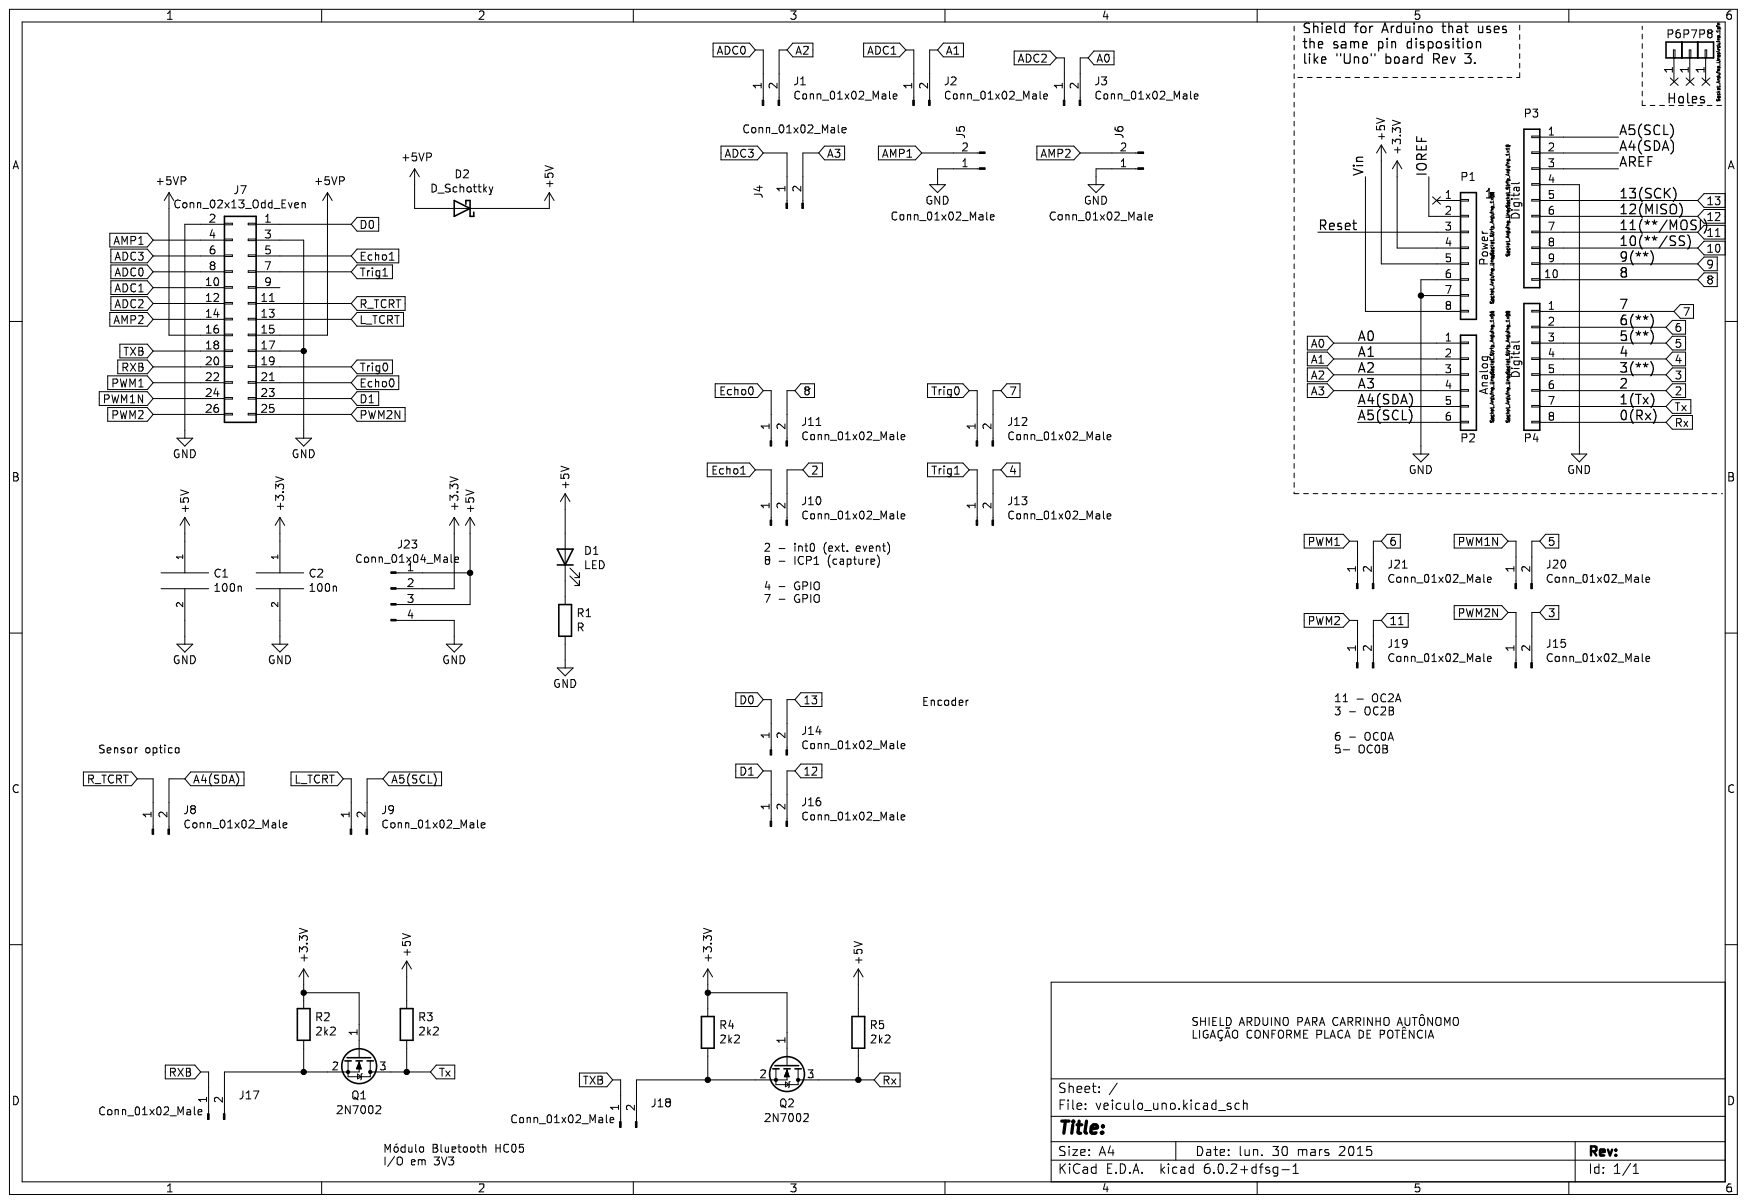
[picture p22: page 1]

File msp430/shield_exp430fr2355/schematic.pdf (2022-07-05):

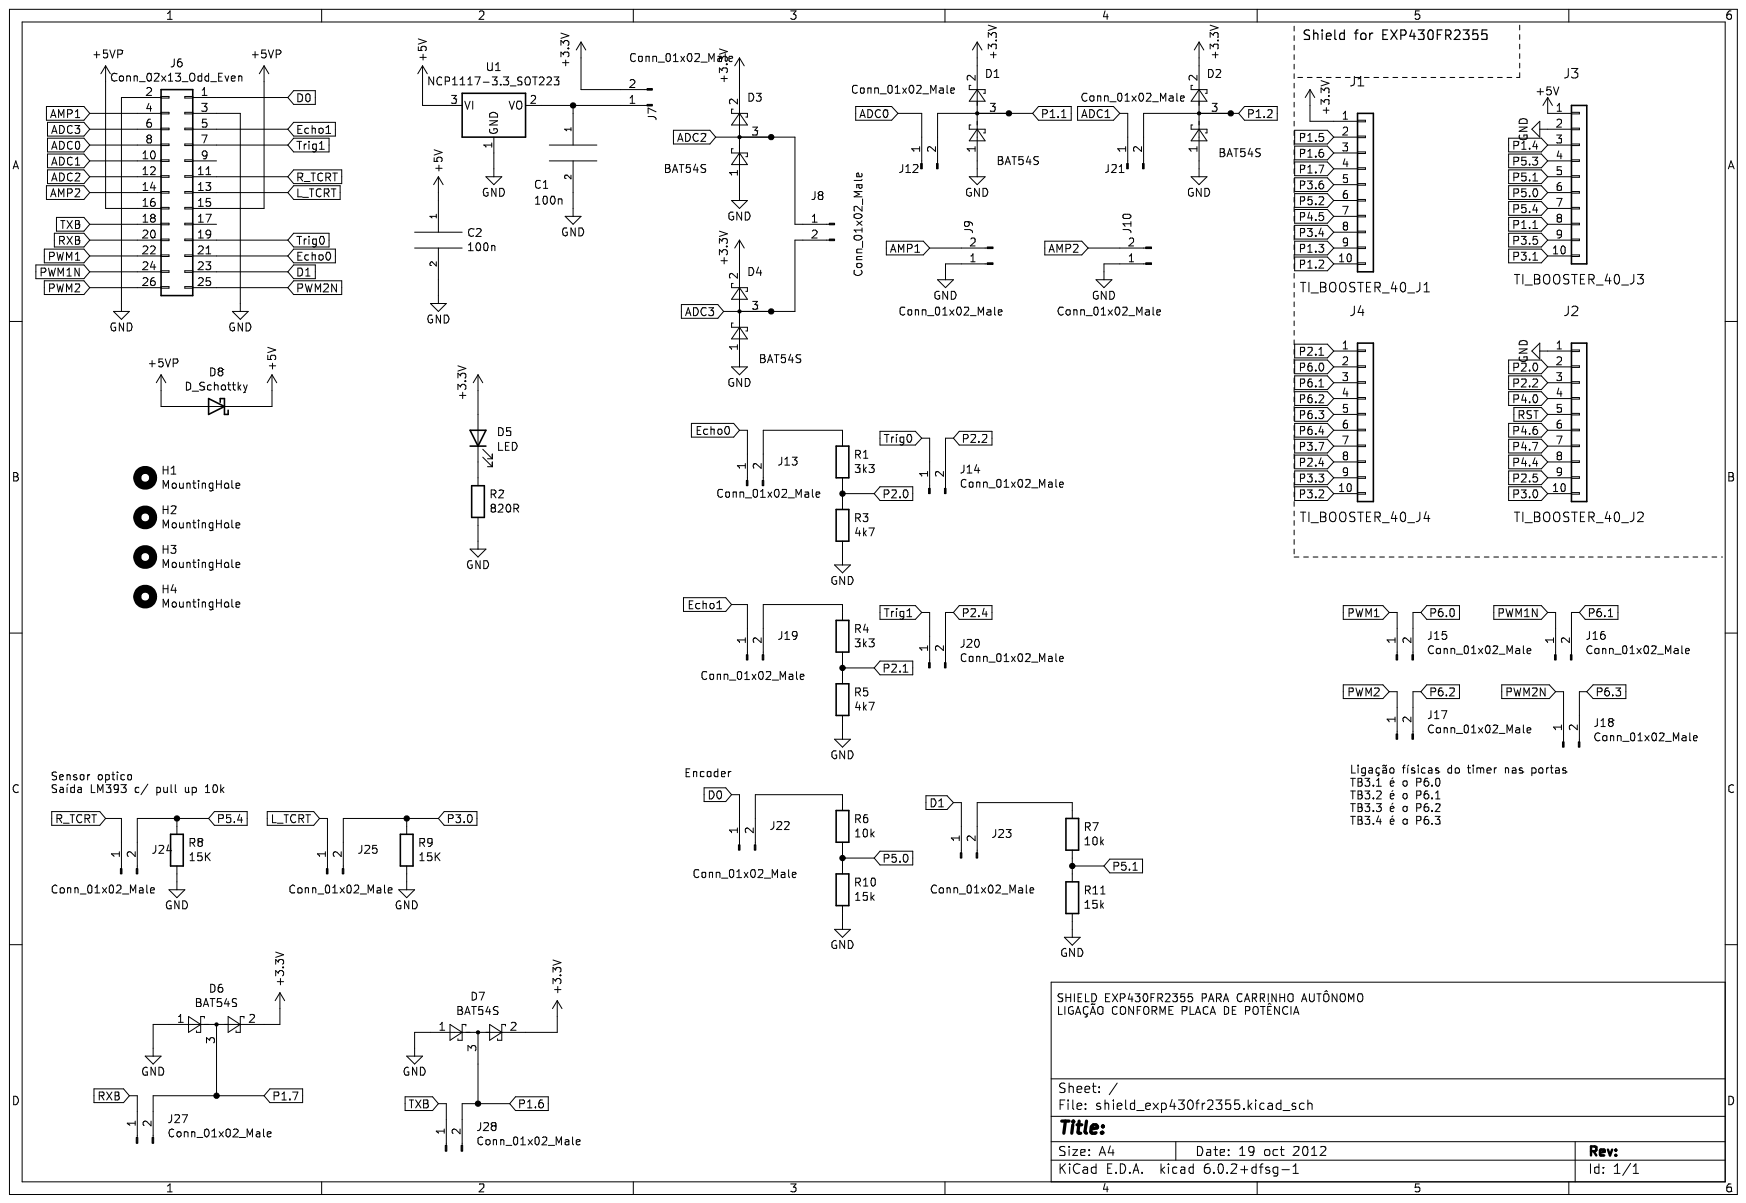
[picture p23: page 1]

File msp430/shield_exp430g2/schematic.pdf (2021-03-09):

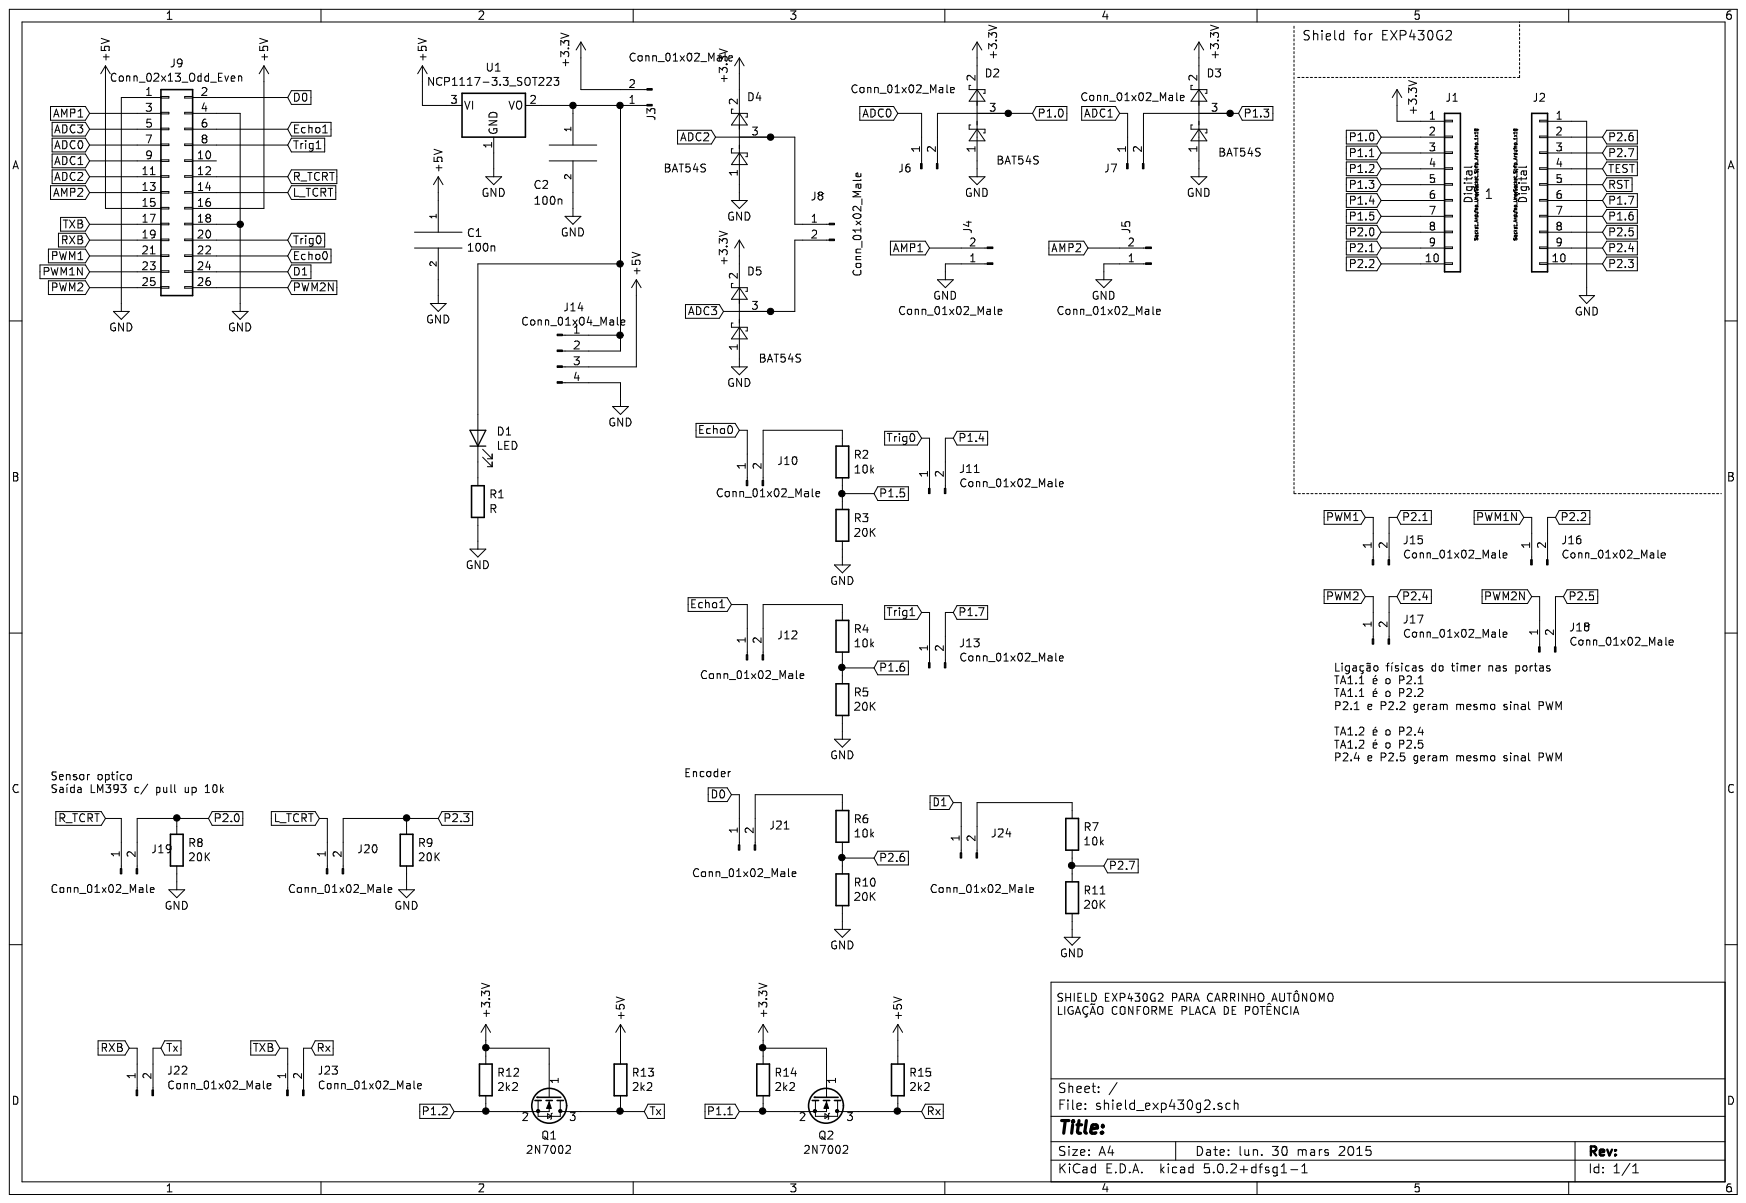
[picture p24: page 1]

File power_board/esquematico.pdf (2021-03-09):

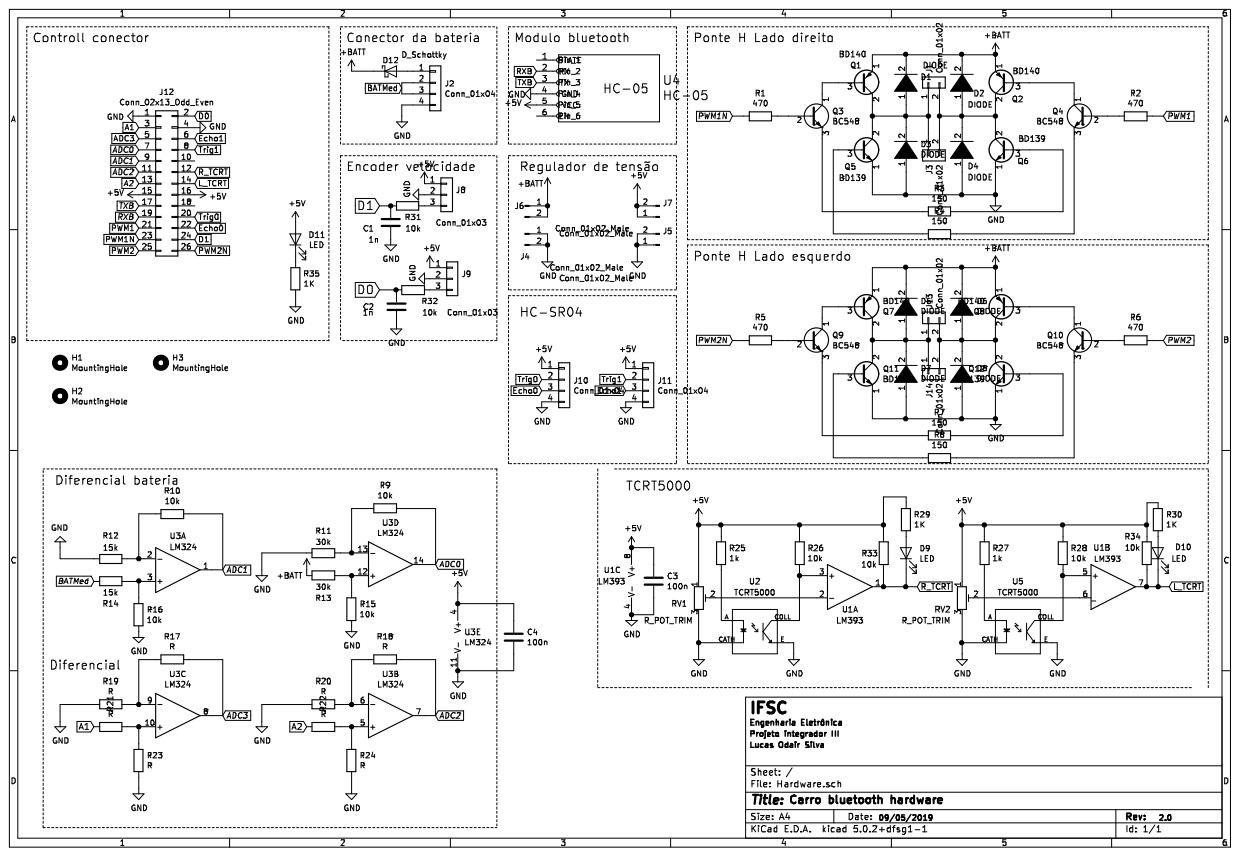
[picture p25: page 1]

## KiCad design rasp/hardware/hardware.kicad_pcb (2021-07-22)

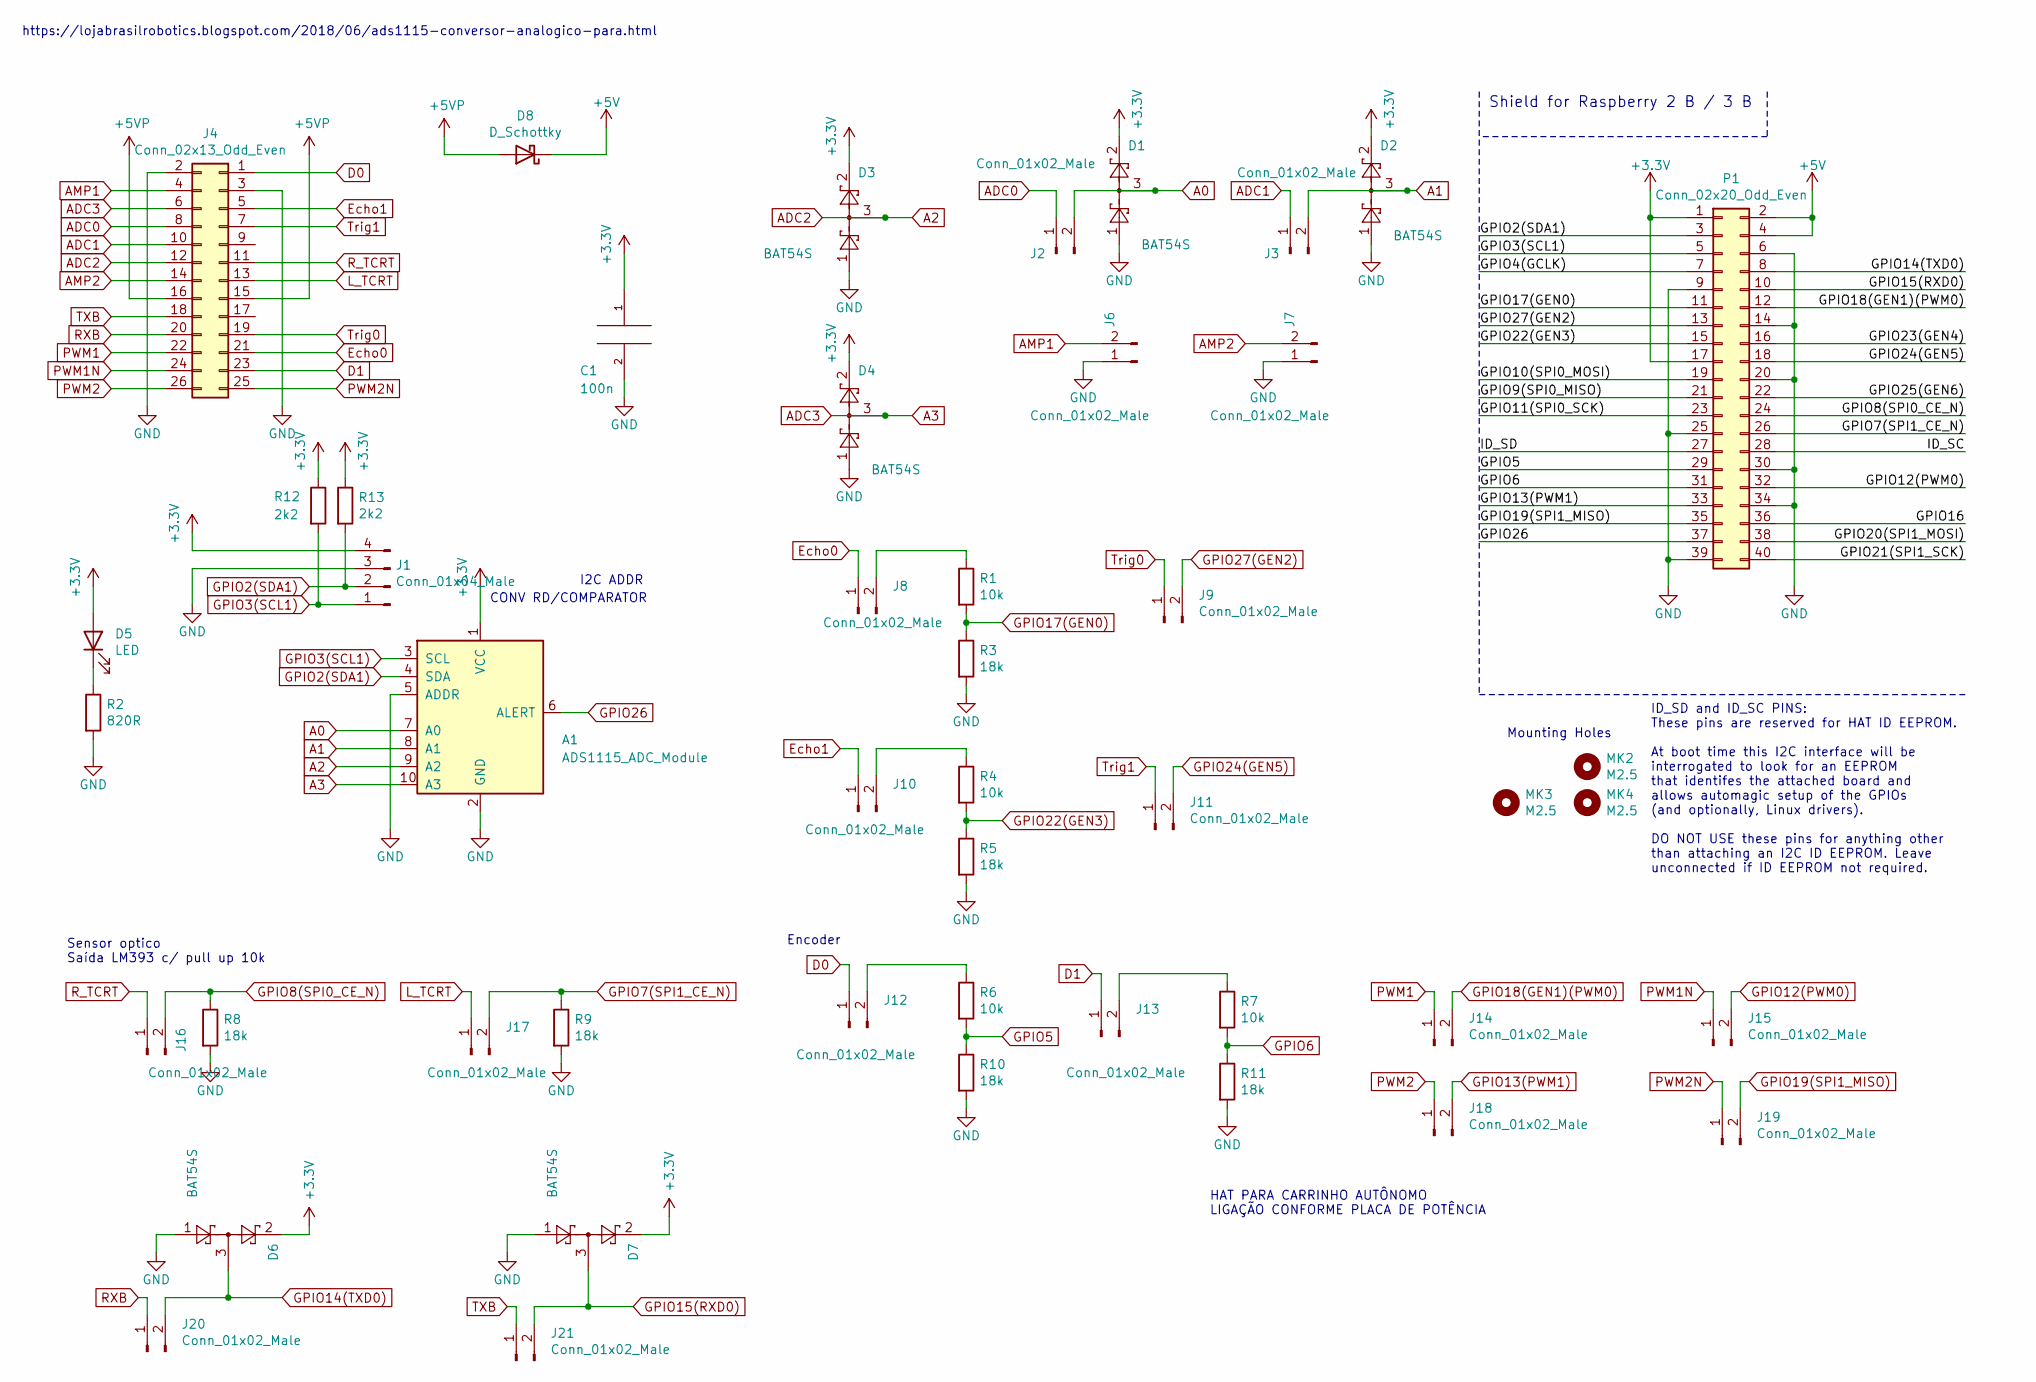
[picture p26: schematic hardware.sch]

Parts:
A1: ADS1115_ADC_Module; ADC1115_ADC_Module
C1: 100n; C_0805_2012Metric_Pad1.15x1.40mm_HandSolder
D1, D2, D3, D4, D6, D7: BAT54S; SOT-23
D5: LED; LED_0805_2012Metric
D8: D_Schottky; D_SMB
J1: Conn_01x04_Male; PinHeader_1x04_P2.54mm_Horizontal
J2, J3, J6, J7, J8, J9, J10, J11, J12, J13, J14, J15, J16, J17, J18, J19, J20, J21: Conn_01x02_Male; PinHeader_1x02_P2.54mm_Vertical
J4: Conn_02x13_Odd_Even; IDC-Header_2x13_P2.54mm_Vertical
MK2, MK3, MK4: M2.5; MountingHole_2.7mm_M2.5
P1: Conn_02x20_Odd_Even; PinSocket_2x20_P2.54mm_Vertical
R1, R4, R6, R7: 10k; R_0805_2012Metric
R2: 820R; R_0805_2012Metric
R3, R5, R8, R9, R10, R11: 18k; R_0805_2012Metric
R12, R13: 2k2; R_0805_2012Metric

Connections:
+3V3: A1.1 (VCC), C1.1, D1.2, D2.2, D3.2, D4.2, D5.2 (A), D6.2, D7.2, J1.4, P1.1, P1.17, R12.1, R13.1
+5V: D8.1 (K), P1.2, P1.4
+5VP: D8.2 (A), J4.15, J4.16
/GPIO4(GCLK): P1.7
/GPIO9(SPI0_MISO): P1.21
/GPIO10(SPI0_MOSI): P1.19
/GPIO11(SPI0_SCK): P1.23
/GPIO16: P1.36
/GPIO20(SPI1_MOSI): P1.38
/GPIO21(SPI1_SCK): P1.40
/GPIO23(GEN4): P1.16
/GPIO25(GEN6): P1.22
/ID_SC: P1.28
/ID_SD: P1.27
A0: A1.7 (A0), D1.3, J2.2
A1: A1.8 (A1), D2.3, J3.2
A2: A1.9 (A2), D3.3, J4.12
A3: A1.10 (A3), D4.3, J4.6
ADC0: J2.1, J4.8
ADC1: J3.1, J4.10
AMP1: J4.4, J6.2
AMP2: J4.14, J7.2
D0: J4.1, J12.1
D1: J4.23, J13.1
Echo0: J4.21, J8.1
Echo1: J4.5, J10.1
GND: A1.2 (GND), A1.5 (ADDR), C1.2, D1.1, D2.1, D3.1, D4.1, D6.1, D7.1, J1.3, J4.2, J4.3, J6.1, J7.1, P1.6, P1.9, P1.14, P1.20, P1.25, P1.30, P1.34, P1.39, R2.2, R3.2, R5.2, R8.2, R9.2, R10.2, R11.2
GPIO2(SDA1): A1.4 (SDA), J1.2, P1.3, R13.2
GPIO3(SCL1): A1.3 (SCL), J1.1, P1.5, R12.2
GPIO5: P1.29, R6.2, R10.1
GPIO6: P1.31, R7.2, R11.1
GPIO7(SPI1_CE_N): J17.2, P1.26, R9.1
GPIO8(SPI0_CE_N): J16.2, P1.24, R8.1
GPIO12(PWM0): J15.2, P1.32
GPIO13(PWM1): J18.2, P1.33
GPIO14(TXD0): D6.3, J20.2, P1.8
GPIO15(RXD0): D7.3, J21.2, P1.10
GPIO17(GEN0): P1.11, R1.2, R3.1
GPIO18(GEN1)(PWM0): J14.2, P1.12
GPIO19(SPI1_MISO): J19.2, P1.35
GPIO22(GEN3): P1.15, R4.2, R5.1
GPIO24(GEN5): J11.2, P1.18
GPIO26: A1.6 (ALERT), P1.37
GPIO27(GEN2): J9.2, P1.13
L_TCRT: J4.13, J17.1
unnamed: D5.1 (K), R2.1
unnamed: J8.2, R1.1
unnamed: J10.2, R4.1
unnamed: J12.2, R6.1
unnamed: J13.2, R7.1
PWM1: J4.22, J14.1
PWM1N: J4.24, J15.1
PWM2: J4.26, J18.1
PWM2N: J4.25, J19.1
RXB: J4.20, J20.1
R_TCRT: J4.11, J16.1
TXB: J4.18, J21.1
Trig0: J4.19, J9.1
Trig1: J4.7, J11.1

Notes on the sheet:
ID_SD and ID_SC PINS: These pins are reserved for HAT ID EEPROM. At boot time this I2C interface will be interrogated to look for an EEPROM that identifes the attached board and allows automagic setup of the GPIOs (and optionally, Linux drivers). DO NOT USE these pins for anything other than attach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
Mounting Holes
Shield for Raspberry 2 B / 3 B
Encoder
Sensor optico Saída LM393 c/ pull up 10k
HAT PARA CARRINHO AUTÔNOMO LIGAÇÃO CONFORME PLACA DE POTÊNCIA
https://lojabrasilrobotics.blogspot.com/2018/06/ads1115-conversor-analogico-para.html
I2C ADDR
CONV RD/COMPARATOR

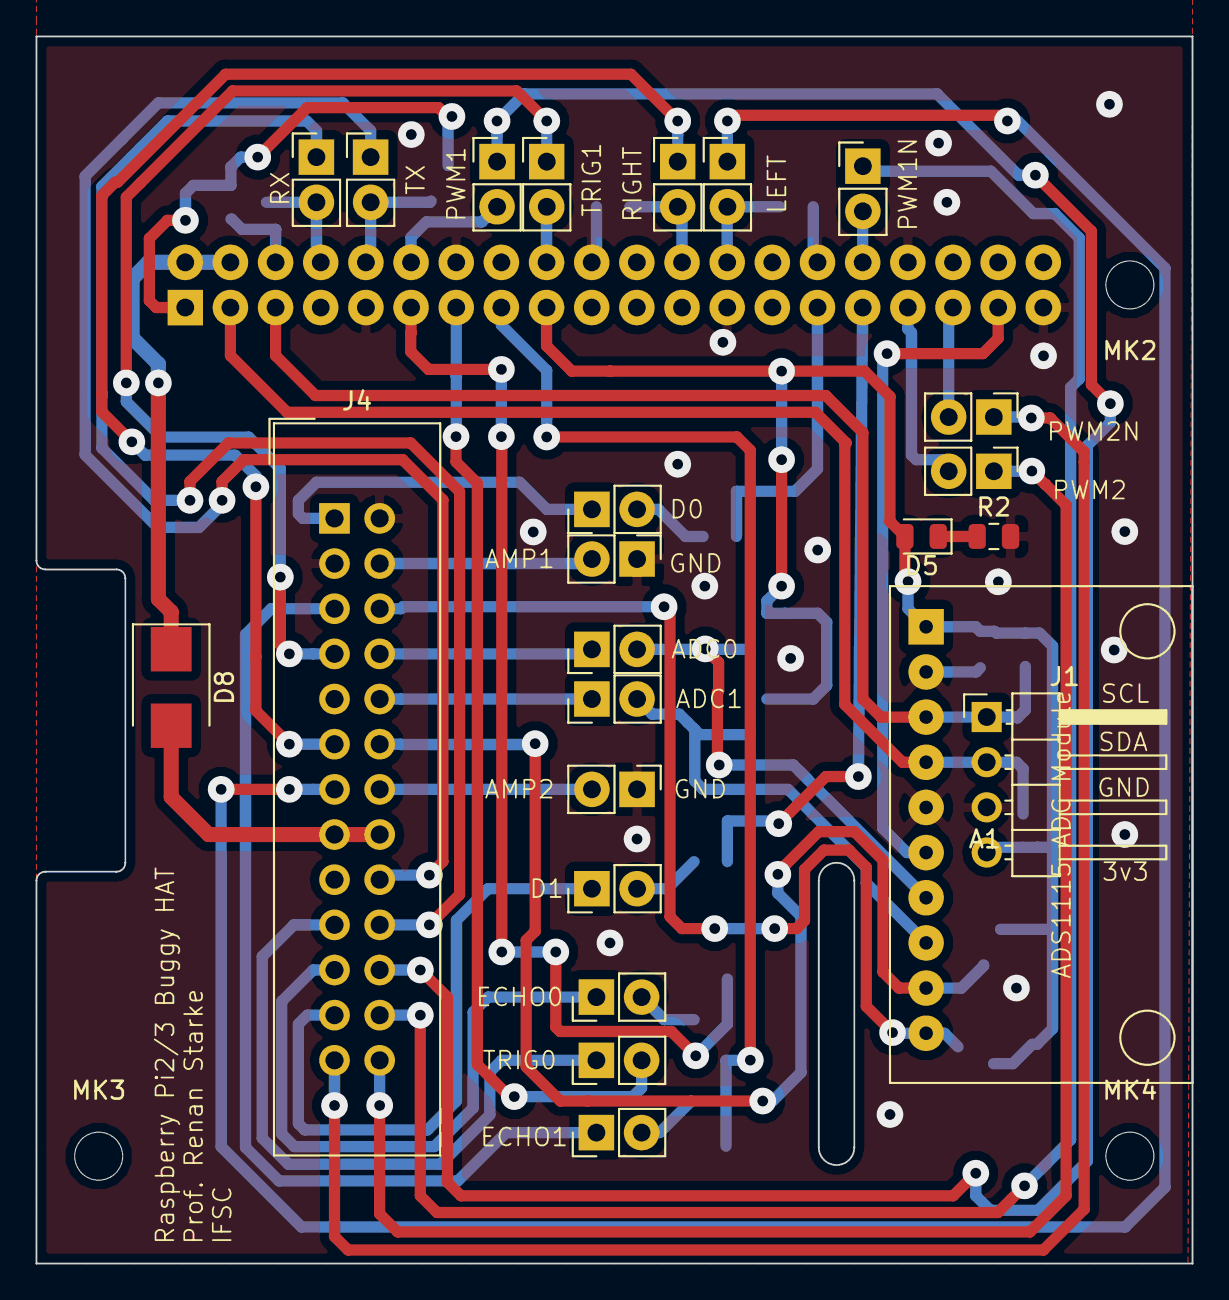
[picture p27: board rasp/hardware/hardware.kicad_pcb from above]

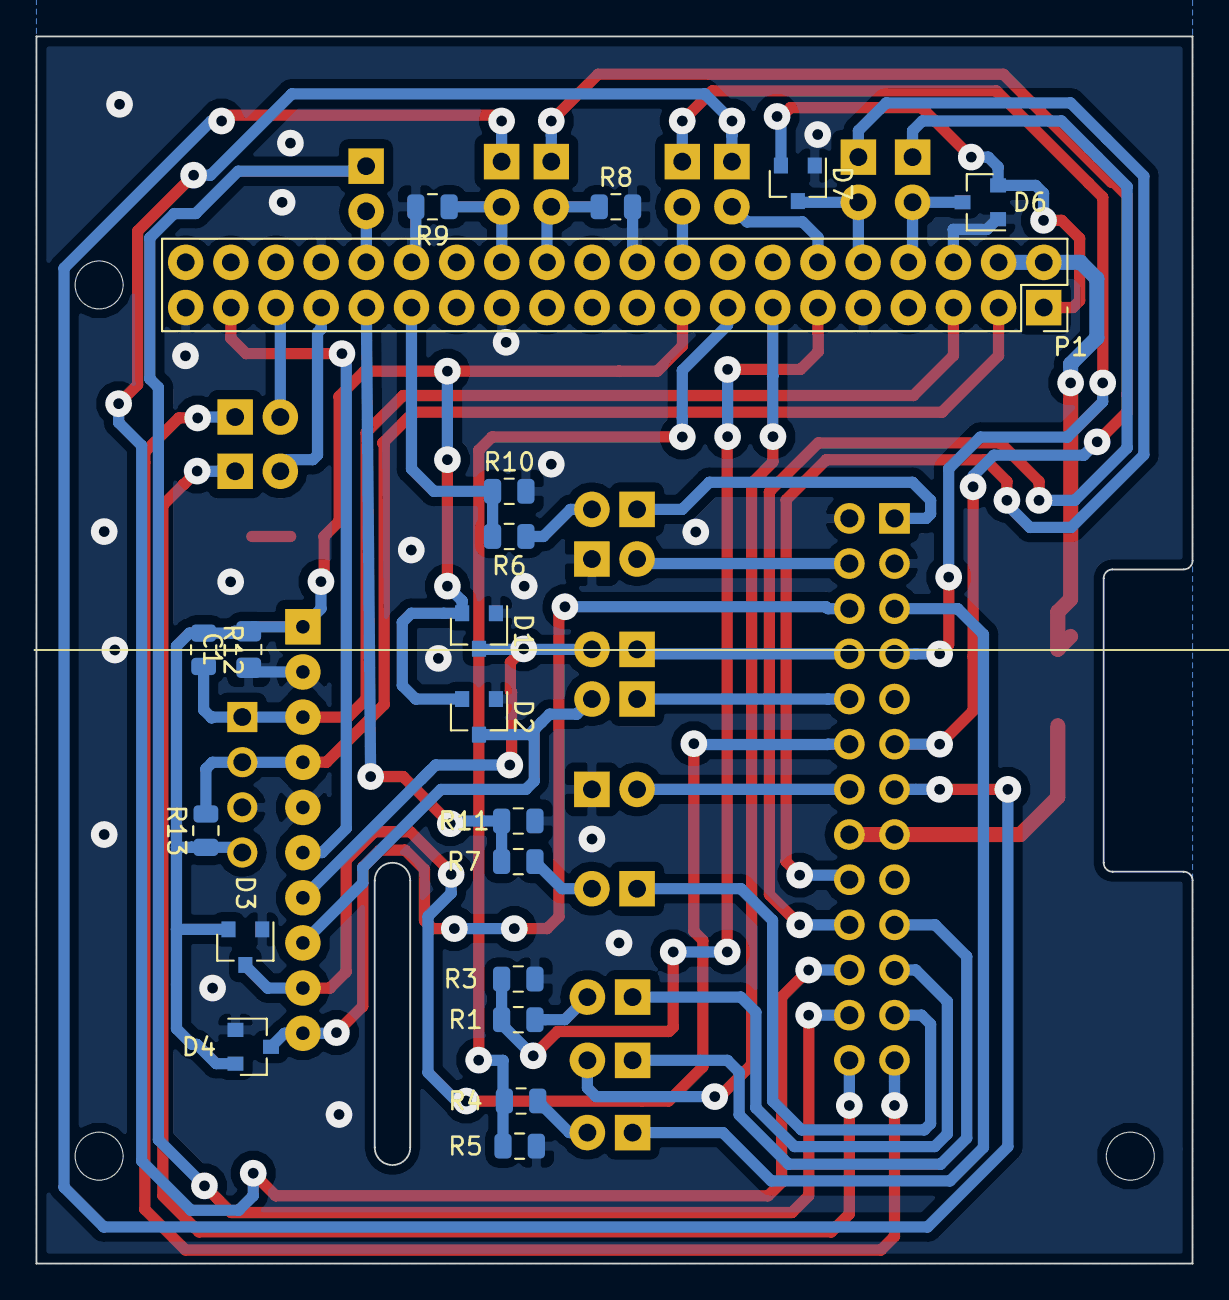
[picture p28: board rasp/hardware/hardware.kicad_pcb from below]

Board: 2 copper layers, 65.0 x 69.0 mm, 47 parts (20 on the bottom side), 48 nets.

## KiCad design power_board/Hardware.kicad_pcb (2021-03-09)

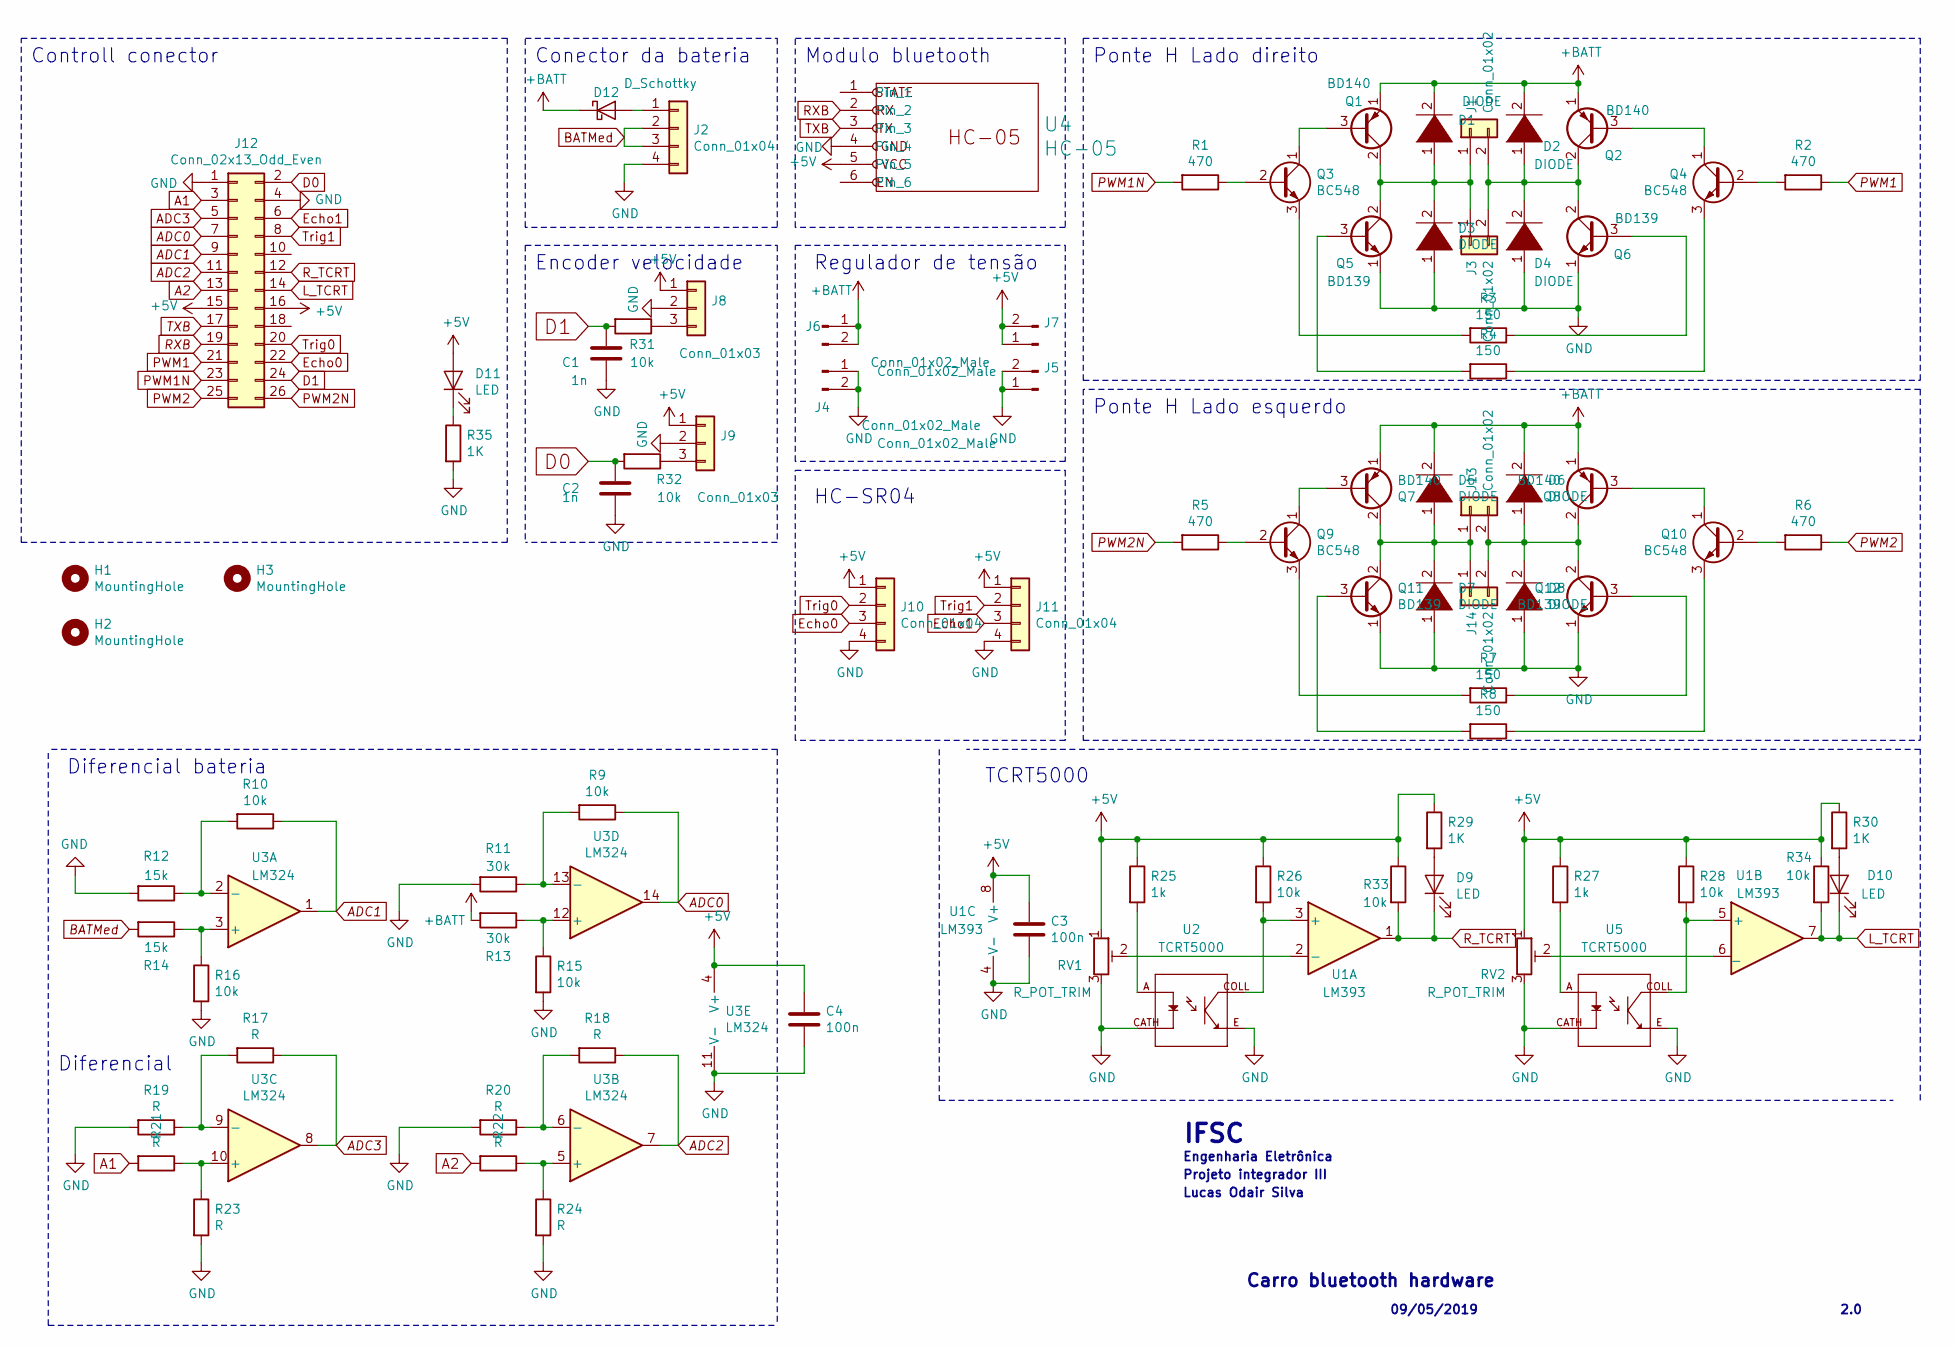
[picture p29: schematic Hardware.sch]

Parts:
C1, C2: 1n; C_0805_2012Metric_Pad1.15x1.40mm_HandSolder
C3, C4: 100n; C_0805_2012Metric
D1, D2, D3, D4, D5, D6, D7, D8: DIODE; D_A-405_P2.54mm_Vertical_AnodeUp
D9, D10, D11: LED; LED_0805_2012Metric
D12: D_Schottky; D_SMB
H1, H2, H3: MountingHole; MountingHole_3.2mm_M3
J1, J3, J13, J14: Conn_01x02; PinHeader_1x02_P2.54mm_Vertical
J2, J10, J11: Conn_01x04; PinHeader_1x04_P2.54mm_Vertical
J4, J5, J6, J7: Conn_01x02_Male; PinSocket_1x02_P2.54mm_Vertical
J8, J9: Conn_01x03; PinHeader_1x03_P2.54mm_Vertical
J12: Conn_02x13_Odd_Even; PinSocket_2x13_P2.54mm_Vertical
Q1, Q2, Q7, Q8: BD140; TO-126-3_Vertical
Q3, Q4, Q9, Q10: BC548; TO-92_Inline_Wide
Q5, Q6, Q11, Q12: BD139; TO-126-3_Vertical
R1, R2, R5, R6: 470; R_0805_2012Metric
R3, R4, R7, R8: 150; R_0805_2012Metric
R9, R10, R15, R16, R26, R28: 10k; R_0805_2012Metric
R11, R13: 30k; R_0805_2012Metric
R12, R14: 15k; R_0805_2012Metric
R17, R18, R19, R20, R21, R22, R23, R24: R; R_0805_2012Metric
R25, R27: 1k; R_0805_2012Metric
R29, R30, R35: 1K; R_0805_2012Metric
R31, R32, R33, R34: 10k; R_0805_2012Metric_Pad1.15x1.40mm_HandSolder
RV1, RV2: R_POT_TRIM; Potentiometer_Piher_PT-6-V_Vertical
U1: LM393
U2, U5: TCRT5000; OPTO_TCRT5000
U3: LM324
U4: HC-05; PinHeader_1x06_P2.54mm_Horizontal

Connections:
+5V: C3.1, C4.1, D11.2 (A), J7.1, J7.2, J8.1, J9.1, J10.1, J11.1, J12.15, J12.16, R25.1, R26.1, R27.1, R28.1, R29.1, R30.1, R33.1, R34.1, RV1.1, RV2.1, U1.8 (V+), U3.4 (V+), U4.5
+BATT: D1.2 (A), D2.2 (A), D5.2 (A), D6.2 (A), D12.1 (K), J6.1, J6.2, Q1.1 (E), Q2.1 (E), Q7.1 (E), Q8.1 (E), R13.2
A1: J12.3, R21.2
A2: J12.13, R22.2
ADC0: J12.7, R9.1, U3.14
ADC1: J12.9, R10.1, U3.1
ADC2: J12.11, R18.1, U3.7
ADC3: J12.5, R17.1, U3.8
BATMed: J2.2, J2.3, R14.2
D0: C2.1, J12.2, R32.2
D1: C1.1, J12.24, R31.2
Echo0: J10.3, J12.22
Echo1: J11.3, J12.6
GND: C1.2, C2.2, C3.2, C4.2, D3.1 (K), D4.1 (K), D7.1 (K), D8.1 (K), J2.4, J4.1, J4.2, J5.1, J5.2, J8.2, J9.2, J10.4, J11.4, J12.1, J12.4, Q5.1 (E), Q6.1 (E), Q11.1 (E), Q12.1 (E), R11.2, R12.2, R15.2, R16.2, R19.2, R20.2, R23.2, R24.2, R35.2, RV1.3, RV2.3, U1.4 (V-), U2.CATH, U2.E, U3.11 (V-), U4.4, U5.CATH, U5.E
L_TCRT: D10.1 (K), J12.14, R34.2, U1.7
unnamed: D1.1 (K), D3.2 (A), J1.1, J3.1, Q1.2 (C), Q5.2 (C)
unnamed: D2.1 (K), D4.2 (A), J1.2, J3.2, Q2.2 (C), Q6.2 (C)
unnamed: D5.1 (K), D7.2 (A), J13.1, J14.1, Q7.2 (C), Q11.2 (C)
unnamed: D6.1 (K), D8.2 (A), J13.2, J14.2, Q8.2 (C), Q12.2 (C)
unnamed: D9.2 (A), R29.2
unnamed: D10.2 (A), R30.2
unnamed: D11.1 (K), R35.1
unnamed: D12.2 (A), J2.1
unnamed: J8.3, R31.1
unnamed: J9.3, R32.1
unnamed: Q1.3 (B), Q3.1 (C)
unnamed: Q2.3 (B), Q4.1 (C)
unnamed: Q3.2 (B), R1.1
unnamed: Q3.3 (E), R3.2
unnamed: Q4.2 (B), R2.2
unnamed: Q4.3 (E), R4.1
unnamed: Q5.3 (B), R4.2
unnamed: Q6.3 (B), R3.1
unnamed: Q7.3 (B), Q9.1 (C)
unnamed: Q9.2 (B), R5.1
unnamed: Q9.3 (E), R7.2
unnamed: Q8.3 (B), Q10.1 (C)
unnamed: Q10.2 (B), R6.2
unnamed: Q10.3 (E), R8.1
unnamed: Q11.3 (B), R8.2
unnamed: Q12.3 (B), R7.1
unnamed: R10.2, R12.1, U3.2 (-)
unnamed: R9.2, R11.1, U3.13 (-)
unnamed: R13.1, R15.1, U3.12 (+)
unnamed: R14.1, R16.1, U3.3 (+)
unnamed: R17.2, R19.1, U3.9 (-)
unnamed: R18.2, R20.1, U3.6 (-)
unnamed: R21.1, R23.1, U3.10 (+)
unnamed: R22.1, R24.1, U3.5 (+)
unnamed: R25.2, U2.A
unnamed: R26.2, U1.3 (+), U2.COLL
unnamed: R27.2, U5.A
unnamed: R28.2, U1.5 (+), U5.COLL
unnamed: RV1.2, U1.2 (-)
unnamed: RV2.2, U1.6 (_)
PWM1: J12.21, R2.1
PWM1N: J12.23, R1.2
PWM2: J12.25, R6.1
PWM2N: J12.26, R5.2
RXB: J12.19, U4.2
R_TCRT: D9.1 (K), J12.12, R33.2, U1.1
TXB: J12.17, U4.3
Trig0: J10.2, J12.20
Trig1: J11.2, J12.8

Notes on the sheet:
Carro bluetooth hardware
09/05/2019
2.0
IFSC
Projeto integrador III
Lucas Odair Silva
Engenharia Eletrônica
Ponte H Lado direito
Ponte H Lado esquerdo
Diferencial bateria
Modulo bluetooth
Conector da bateria
Regulador de tensão
Controll conector
Encoder velocidade
Diferencial
HC-SR04
TCRT5000

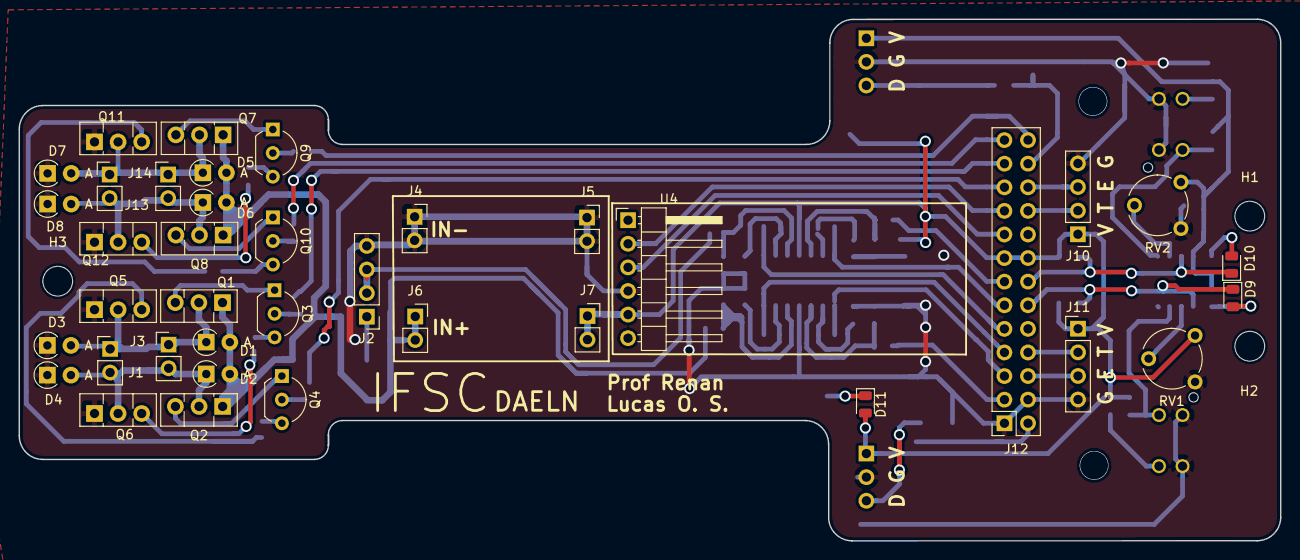
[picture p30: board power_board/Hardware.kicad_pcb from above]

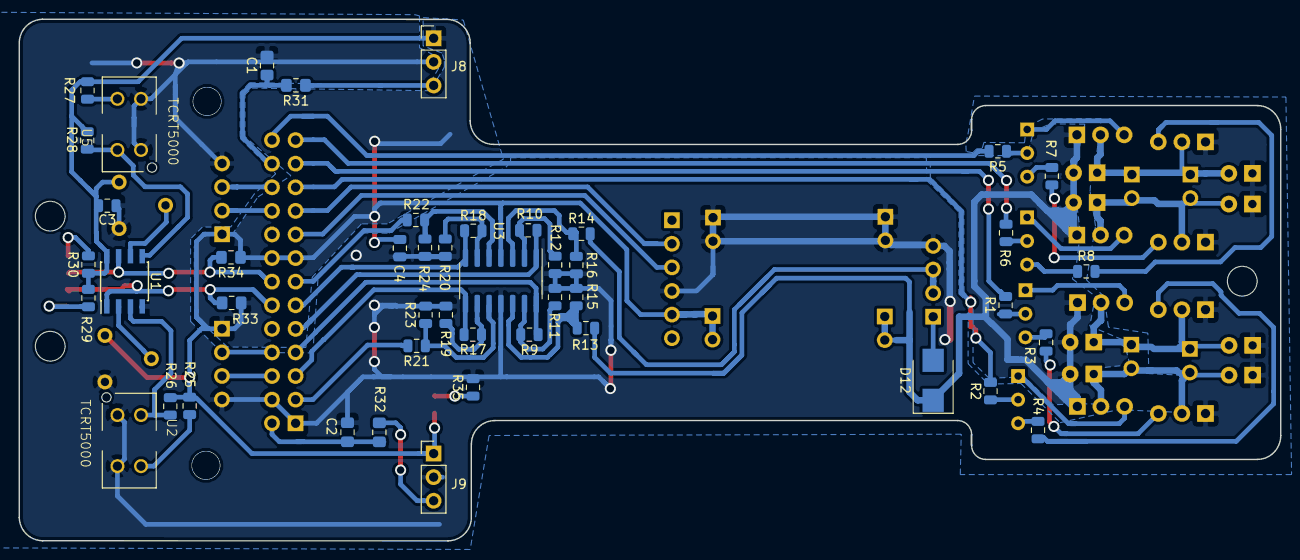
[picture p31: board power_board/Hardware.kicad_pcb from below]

Board: 2 copper layers, 135.8 x 56.1 mm, 87 parts (46 on the bottom side), 64 nets.

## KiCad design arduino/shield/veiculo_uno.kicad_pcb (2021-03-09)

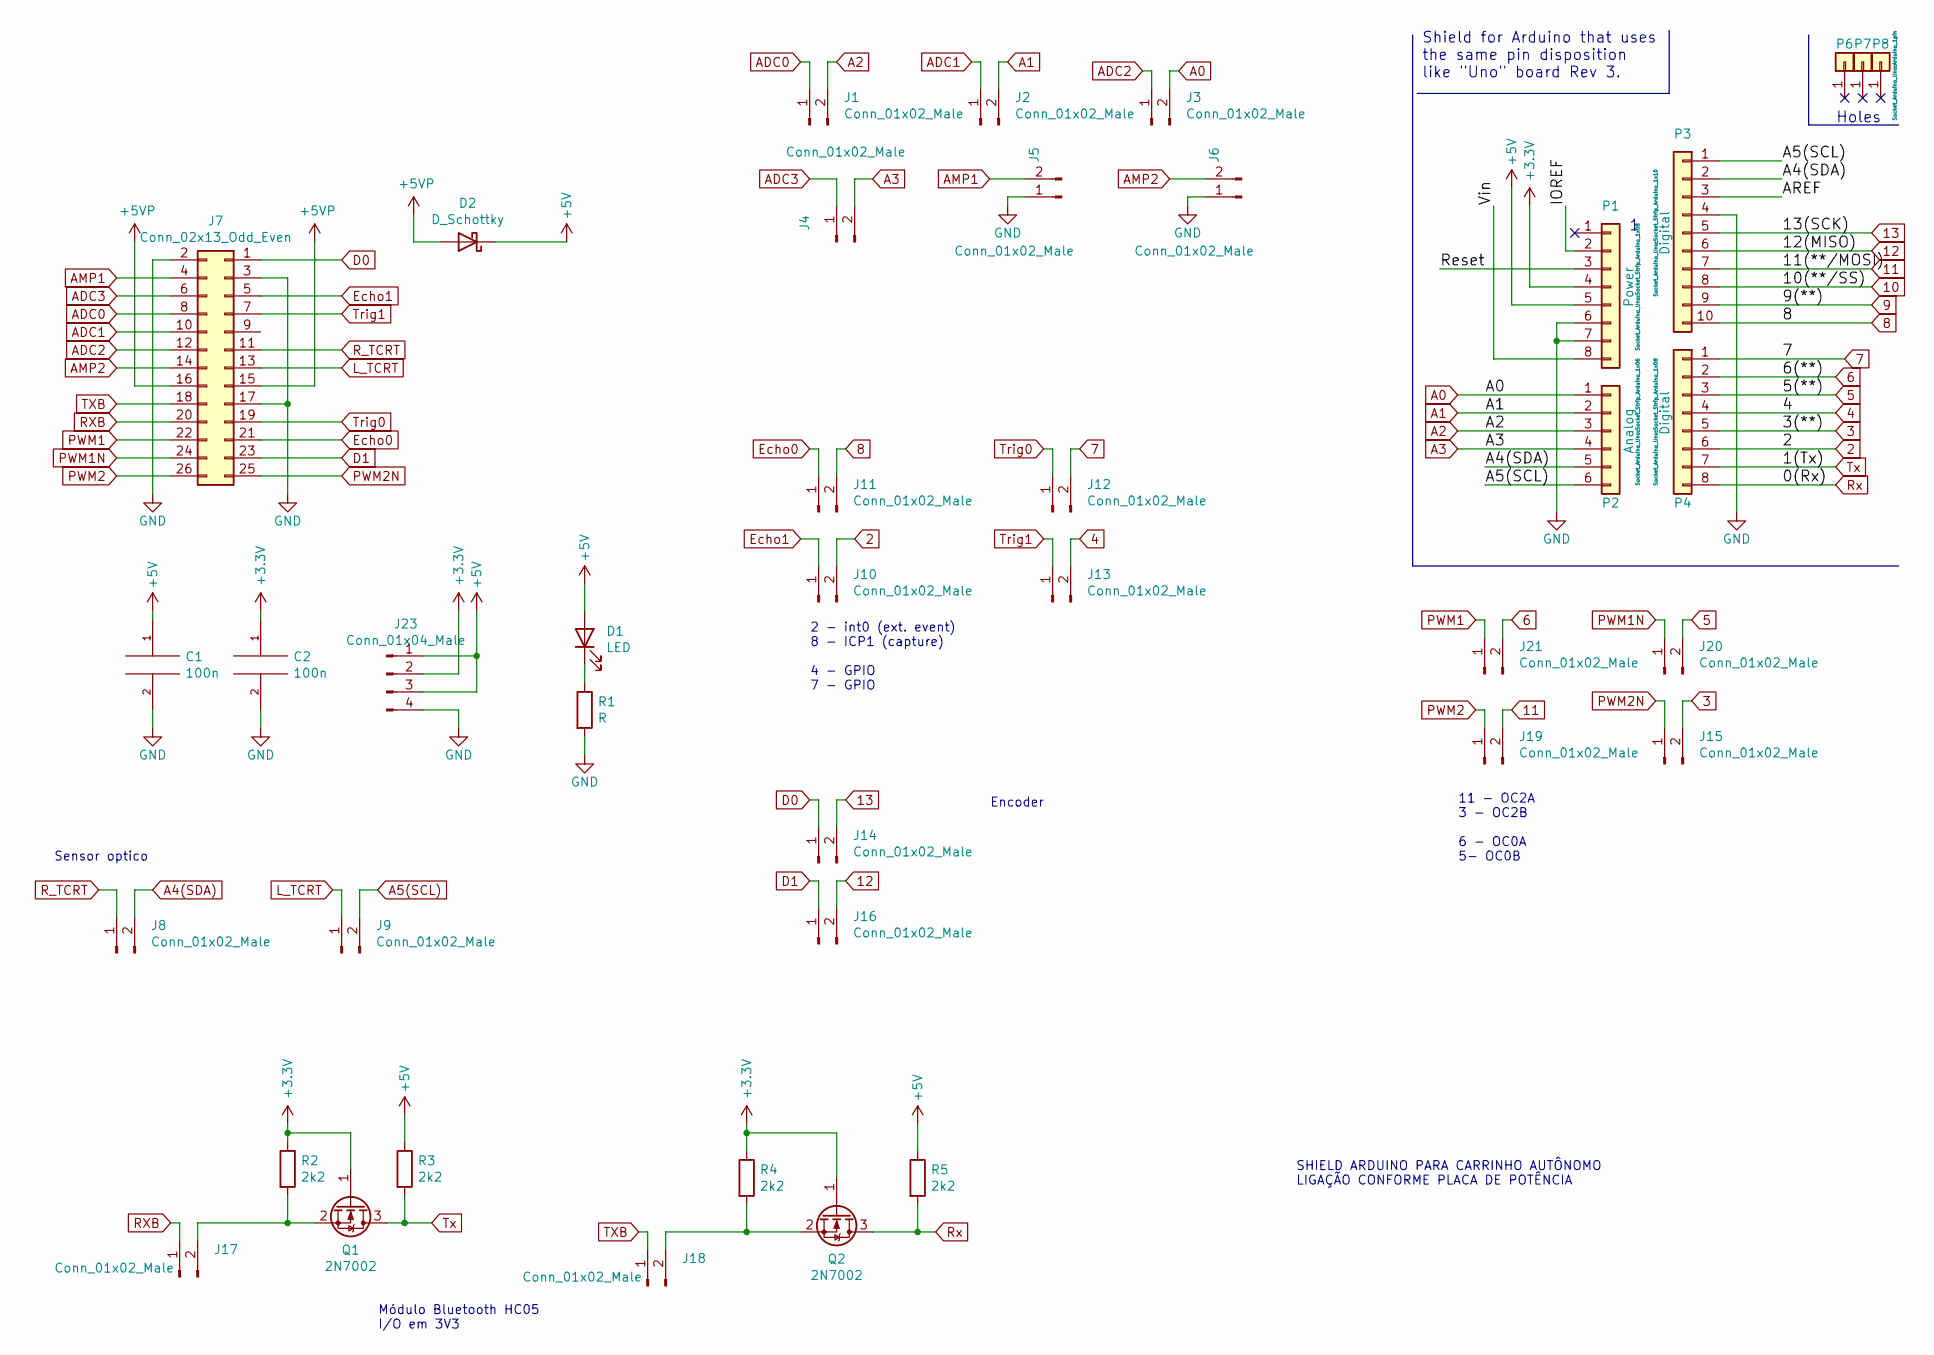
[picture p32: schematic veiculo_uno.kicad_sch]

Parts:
C1, C2: 100n; C_0805_2012Metric_Pad1.15x1.40mm_HandSolder
D1: LED; LED_0805_2012Metric
D2: D_Schottky; D_SMB
J1, J2, J3, J4, J5, J6, J8, J9, J10, J11, J12, J13, J14, J15, J16, J17, J18, J19, J20, J21: Conn_01x02_Male; PinHeader_1x02_P2.54mm_Vertical
J7: Conn_02x13_Odd_Even; IDC-Header_2x13_P2.54mm_Vertical
J23: Conn_01x04_Male; PinHeader_1x04_P2.54mm_Vertical
P1: Power; Socket_Strip_Arduino_1x08
P2: Analog; Socket_Strip_Arduino_1x06
P3: Digital; Socket_Strip_Arduino_1x10
P4: Digital; Socket_Strip_Arduino_1x08
P6, P7, P8: CONN_01X01; Arduino_1pin
Q1, Q2: 2N7002; SOT-23
R1: R; R_0805_2012Metric
R2, R3, R4, R5: 2k2; R_0805_2012Metric

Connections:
2: J10.2, P4.6
3: J15.2, P4.5
4: J13.2, P4.4
5: J20.2, P4.3
6: J21.2, P4.2
7: J12.2, P4.1
8: J11.2, P3.10
9: P3.9
10: P3.8
11: J19.2, P3.7
12: J16.2, P3.6
13: J14.2, P3.5
+3V3: C2.1, J23.2, P1.4, Q1.1 (G), Q2.1 (G), R2.1, R4.1
+5V: C1.1, D1.2 (A), D2.1 (K), J23.1, J23.3, P1.5, R3.1, R5.1
+5VP: D2.2 (A), J7.15, J7.16
/AREF: P3.3
/IOREF: P1.2
/Reset: P1.3
/Vin: P1.8
A0: J3.2, P2.1
A1: J2.2, P2.2
A2: J1.2, P2.3
A3: J4.2, P2.4
A4(SDA): J8.2, P2.5, P3.2
A5(SCL): J9.2, P2.6, P3.1
ADC0: J1.1, J7.8
ADC1: J2.1, J7.10
ADC2: J3.1, J7.12
ADC3: J4.1, J7.6
AMP1: J5.2, J7.4
AMP2: J6.2, J7.14
D0: J7.1, J14.1
D1: J7.23, J16.1
Echo0: J7.21, J11.1
Echo1: J7.5, J10.1
GND: C1.2, C2.2, J5.1, J6.1, J7.2, J7.3, J7.17, J23.4, P1.6, P1.7, P3.4, R1.2
L_TCRT: J7.13, J9.1
unnamed: D1.1 (K), R1.1
unnamed: J17.2, Q1.2 (S), R2.2
unnamed: J18.2, Q2.2 (S), R4.2
PWM1: J7.22, J21.1
PWM1N: J7.24, J20.1
PWM2: J7.26, J19.1
PWM2N: J7.25, J15.1
RXB: J7.20, J17.1
R_TCRT: J7.11, J8.1
Rx: P4.8, Q2.3 (D), R5.2
TXB: J7.18, J18.1
Trig0: J7.19, J12.1
Trig1: J7.7, J13.1
Tx: P4.7, Q1.3 (D), R3.2

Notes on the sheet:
11 - OC2A 3 - OC2B 6 - OC0A 5- OC0B
Módulo Bluetooth HC05 I/O em 3V3
SHIELD ARDUINO PARA CARRINHO AUTÔNOMO LIGAÇÃO CONFORME PLACA DE POTÊNCIA
2 - int0 (ext. event) 8 - ICP1 (capture) 4 - GPIO 7 - GPIO
Encoder
Shield for Arduino that uses the same pin disposition like "Uno" board Rev 3.
Sensor optico
Holes

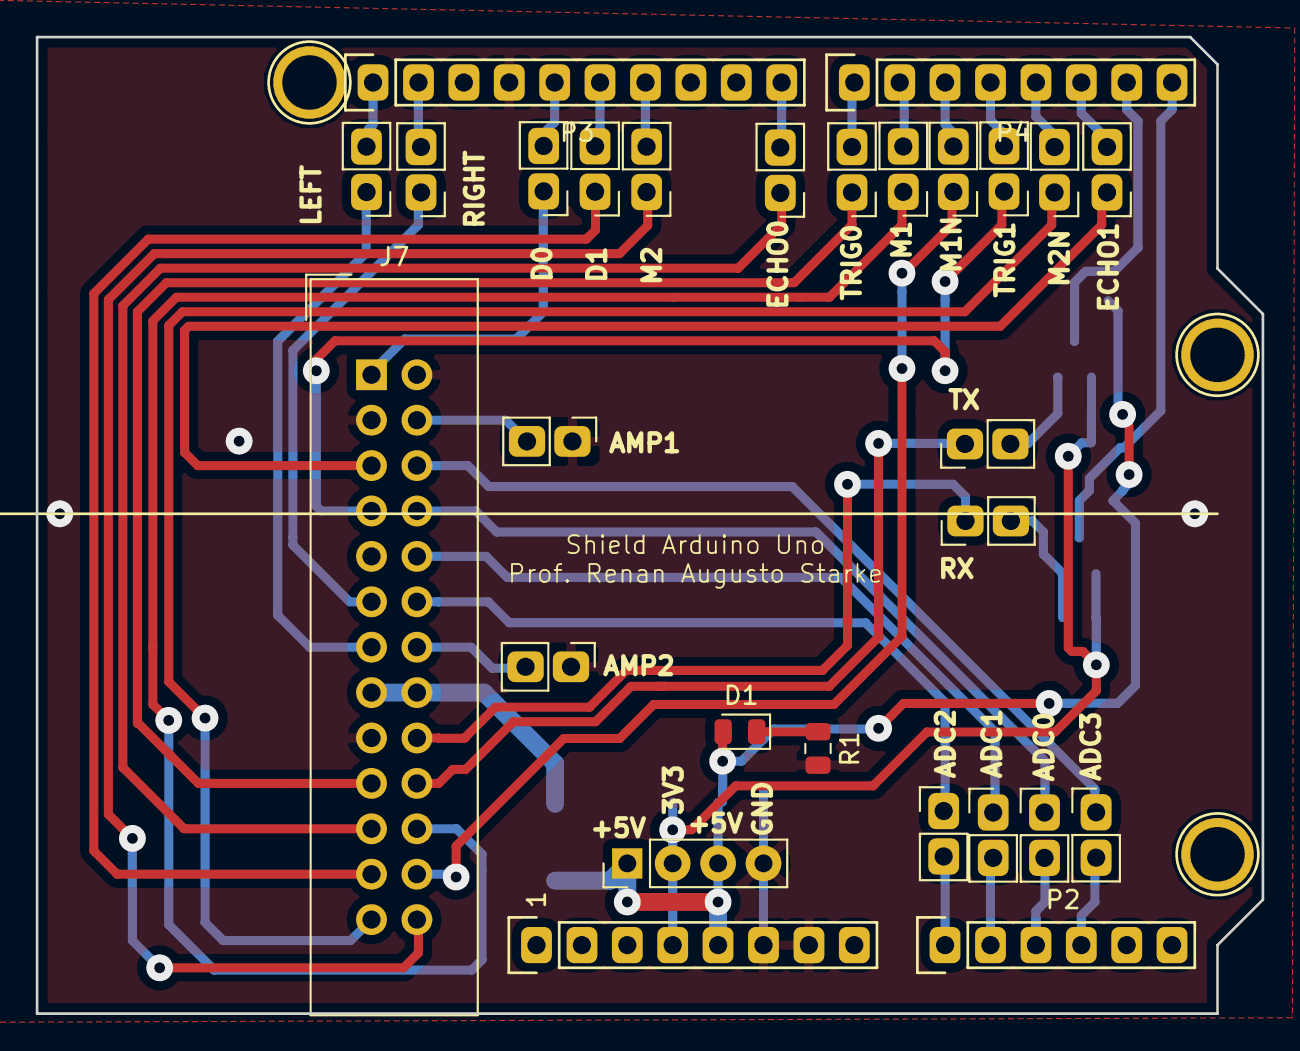
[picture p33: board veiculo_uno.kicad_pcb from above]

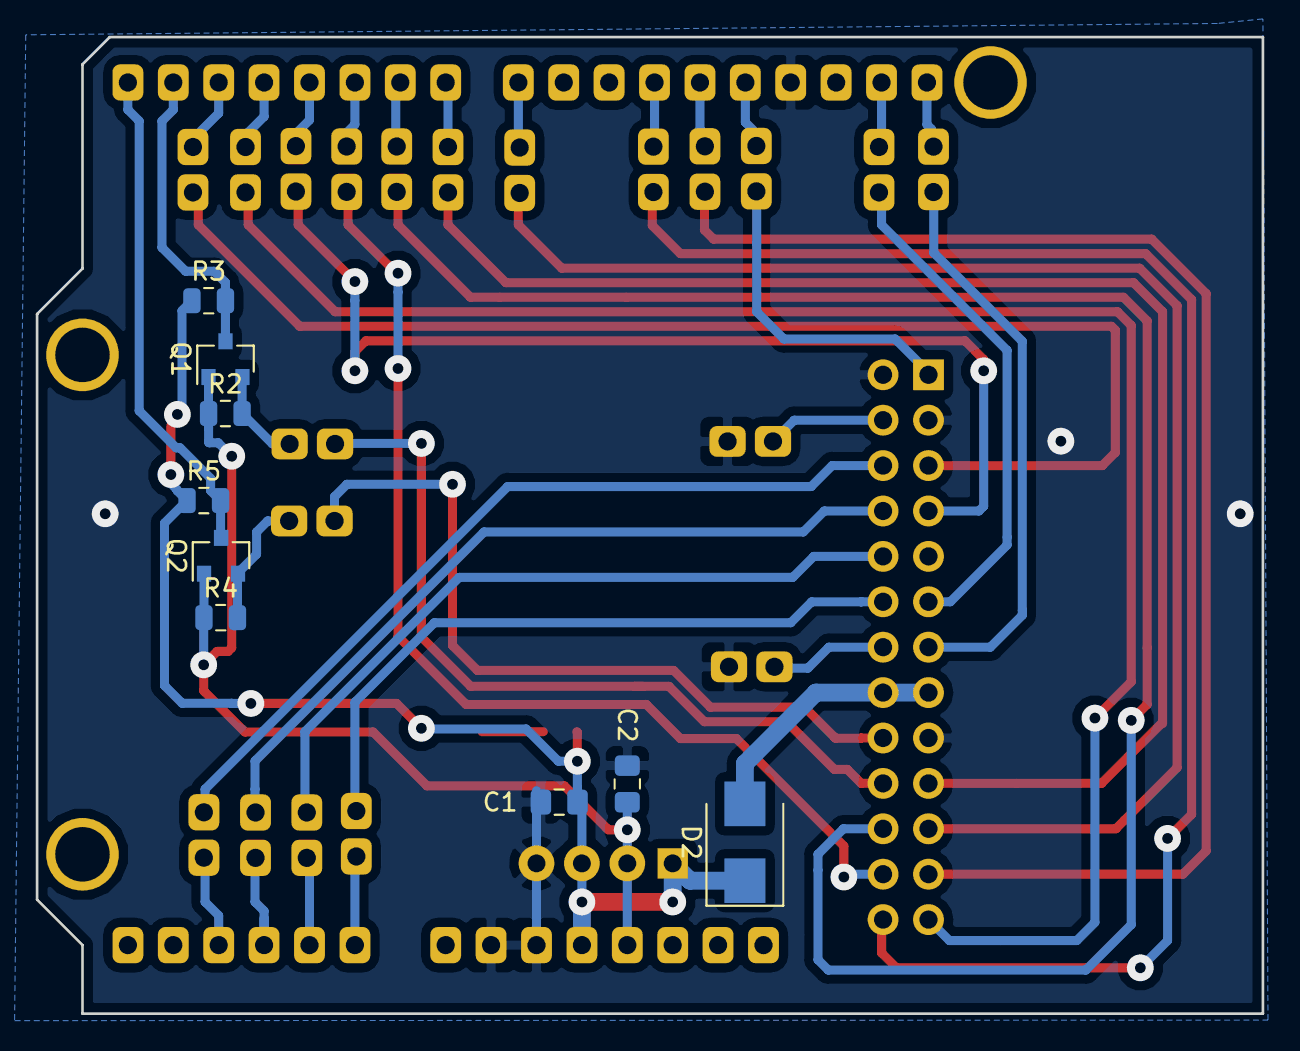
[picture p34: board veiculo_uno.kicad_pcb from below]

Board: 2 copper layers, 68.6 x 54.6 mm, 40 parts (9 on the bottom side), 45 nets.

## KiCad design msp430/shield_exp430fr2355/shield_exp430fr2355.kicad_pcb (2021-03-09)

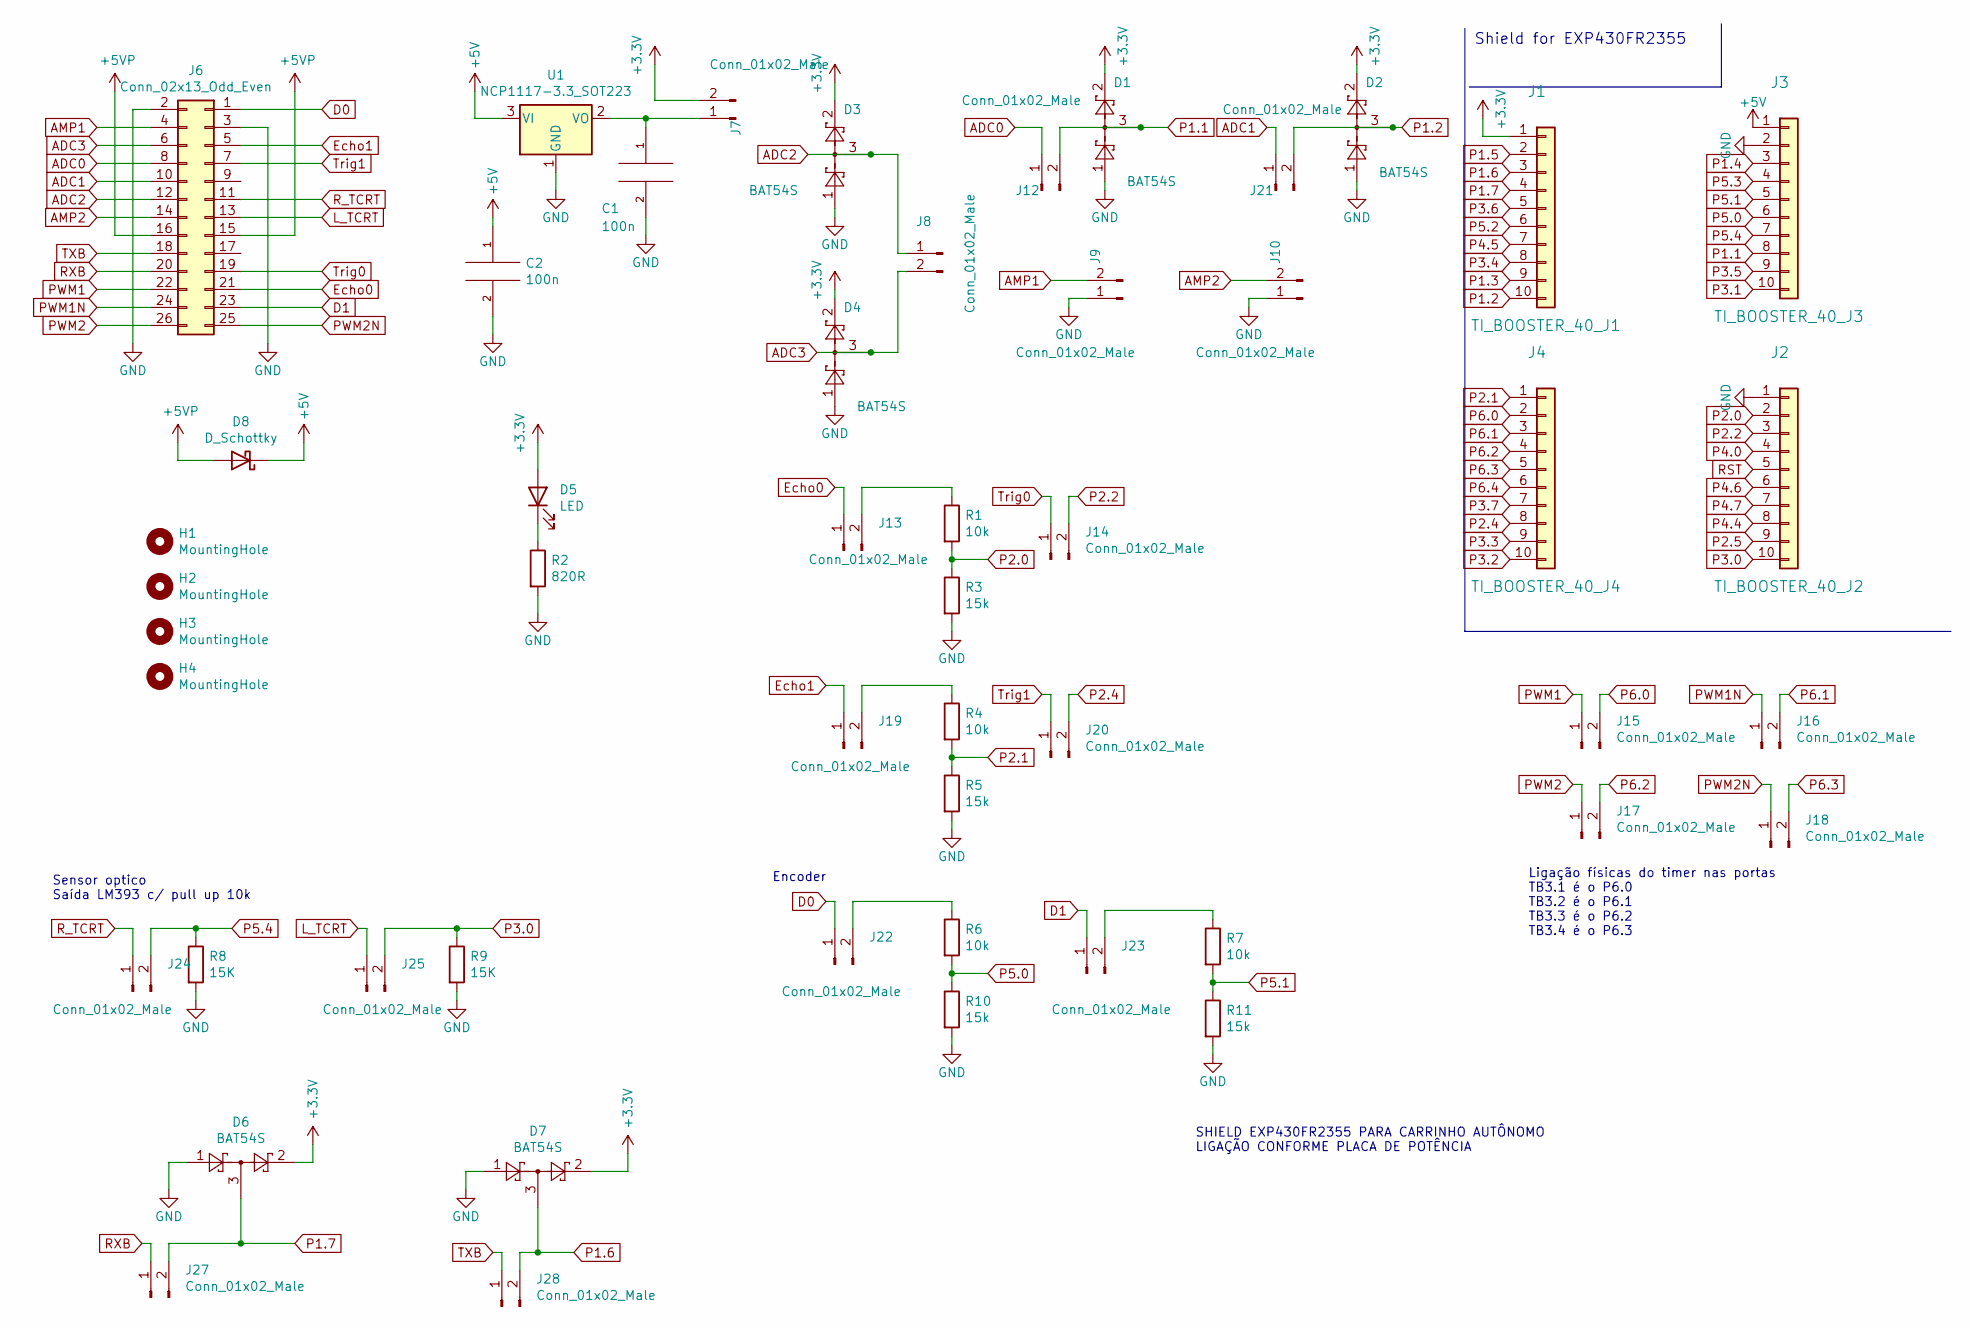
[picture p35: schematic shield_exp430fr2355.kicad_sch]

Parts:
C1, C2: 100n; C_0805_2012Metric_Pad1.15x1.40mm_HandSolder
D1, D2, D3, D4, D6, D7: BAT54S; SOT-23
D5: LED; LED_0805_2012Metric
D8: D_Schottky; D_SMB
H1, H2: MountingHole; MountingHole_2.2mm_M2
H3, H4: MountingHole; MountingHole_3.2mm_M3
J1: TI_BOOSTER_40_J1; PinHeader_1x10_P2.54mm_Vertical
J2: TI_BOOSTER_40_J2; PinHeader_1x10_P2.54mm_Vertical
J3: TI_BOOSTER_40_J3; PinHeader_1x10_P2.54mm_Vertical
J4: TI_BOOSTER_40_J4; PinHeader_1x10_P2.54mm_Vertical
J6: Conn_02x13_Odd_Even; IDC-Header_2x13_P2.54mm_Vertical
J7, J8, J9, J10, J12, J13, J14, J15, J16, J17, J18, J19, J20, J21, J22, J23, J24, J25, J27, J28: Conn_01x02_Male; PinHeader_1x02_P2.54mm_Vertical
R1, R4, R6, R7: 10k; R_0805_2012Metric
R2: 820R; R_0805_2012Metric
R3, R5, R10, R11: 15k; R_0805_2012Metric
R8, R9: 15K; R_0805_2012Metric
U1: NCP1117-3.3_SOT223; SOT-223-3_TabPin2

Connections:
+3V3: D1.2, D2.2, D3.2, D4.2, D5.2 (A), D6.2, D7.2, J1.1, J7.2
+5V: C2.1, D8.1 (K), J3.1, U1.3 (VI)
+5VP: D8.2 (A), J6.15, J6.16
ADC0: J6.8, J12.1
ADC1: J6.10, J21.1
ADC2: D3.3, J6.12, J8.1
ADC3: D4.3, J6.6, J8.2
AMP1: J6.4, J9.2
AMP2: J6.14, J10.2
D0: J6.1, J22.1
D1: J6.23, J23.1
Echo0: J6.21, J13.1
Echo1: J6.5, J19.1
GND: C1.2, C2.2, D1.1, D2.1, D3.1, D4.1, D6.1, D7.1, J2.1, J3.2, J6.2, J6.3, J9.1, J10.1, R2.2, R3.2, R5.2, R8.2, R9.2, R10.2, R11.2, U1.1 (GND)
L_TCRT: J6.13, J25.1
unnamed: C1.1, J7.1, U1.2 (VO)
unnamed: D5.1 (K), R2.1
unnamed: J13.2, R1.1
unnamed: J19.2, R4.1
unnamed: J22.2, R6.1
unnamed: J23.2, R7.1
P1.1: D1.3, J3.8, J12.2
P1.2: D2.3, J1.10, J21.2
P1.3: J1.9
P1.4: J3.3
P1.5: J1.2
P1.6: D7.3, J1.3, J28.2
P1.7: D6.3, J1.4, J27.2
P2.0: J2.2, R1.2, R3.1
P2.1: J4.1, R4.2, R5.1
P2.2: J2.3, J14.2
P2.4: J4.8, J20.2
P2.5: J2.9
P3.0: J2.10, J25.2, R9.1
P3.1: J3.10
P3.2: J4.10
P3.3: J4.9
P3.4: J1.8
P3.5: J3.9
P3.6: J1.5
P3.7: J4.7
P4.0: J2.4
P4.4: J2.8
P4.5: J1.7
P4.6: J2.6
P4.7: J2.7
P5.0: J3.6, R6.2, R10.1
P5.1: J3.5, R7.2, R11.1
P5.2: J1.6
P5.3: J3.4
P5.4: J3.7, J24.2, R8.1
P6.0: J4.2, J15.2
P6.1: J4.3, J16.2
P6.2: J4.4, J17.2
P6.3: J4.5, J18.2
P6.4: J4.6
PWM1: J6.22, J15.1
PWM1N: J6.24, J16.1
PWM2: J6.26, J17.1
PWM2N: J6.25, J18.1
RST: J2.5
RXB: J6.20, J27.1
R_TCRT: J6.11, J24.1
TXB: J6.18, J28.1
Trig0: J6.19, J14.1
Trig1: J6.7, J20.1

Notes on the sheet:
Encoder
SHIELD EXP430FR2355 PARA CARRINHO AUTÔNOMO LIGAÇÃO CONFORME PLACA DE POTÊNCIA
Sensor optico Saída LM393 c/ pull up 10k
Ligação físicas do timer nas portas TB3.1 é o P6.0 TB3.2 é o P6.1 TB3.3 é o P6.2 TB3.4 é o P6.3
Shield for EXP430FR2355

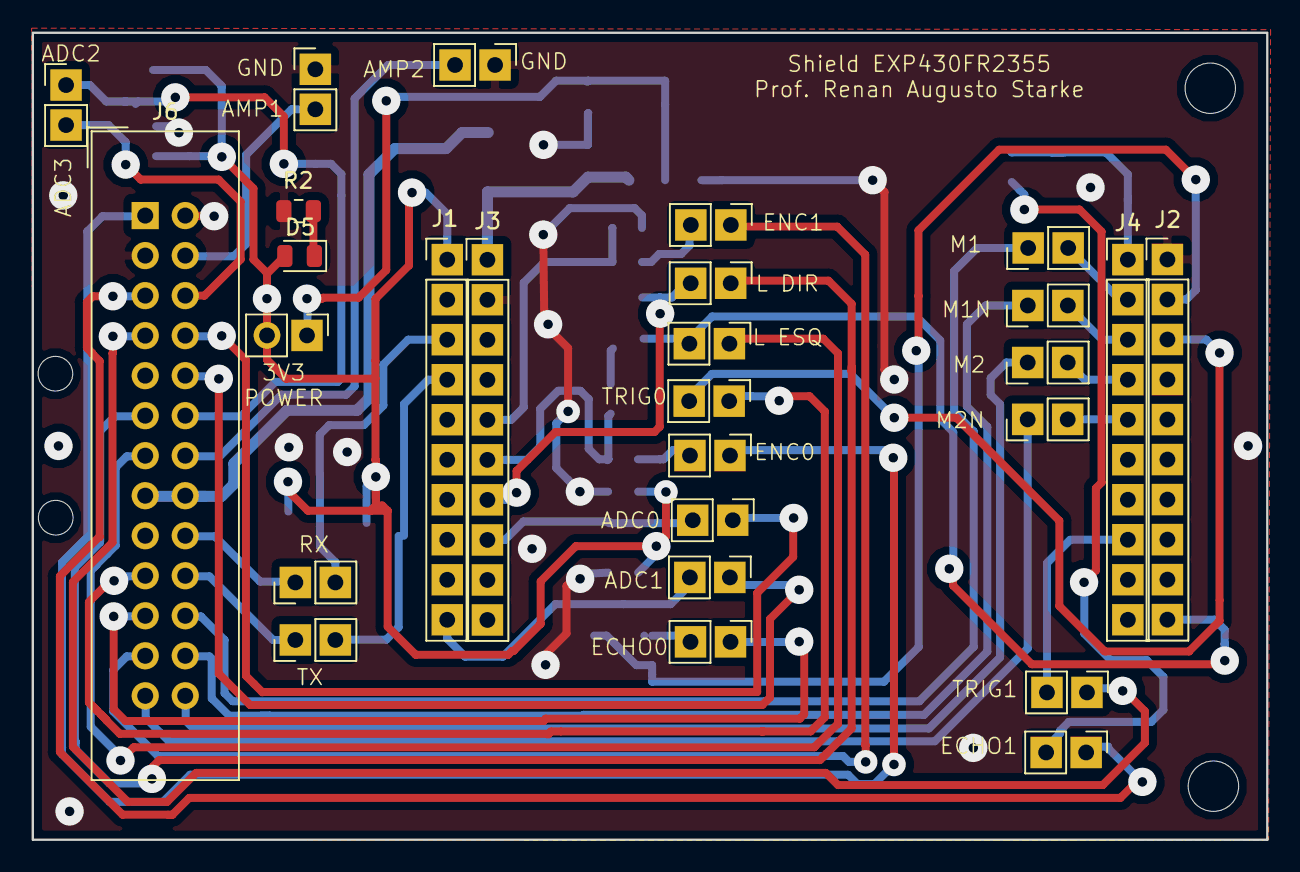
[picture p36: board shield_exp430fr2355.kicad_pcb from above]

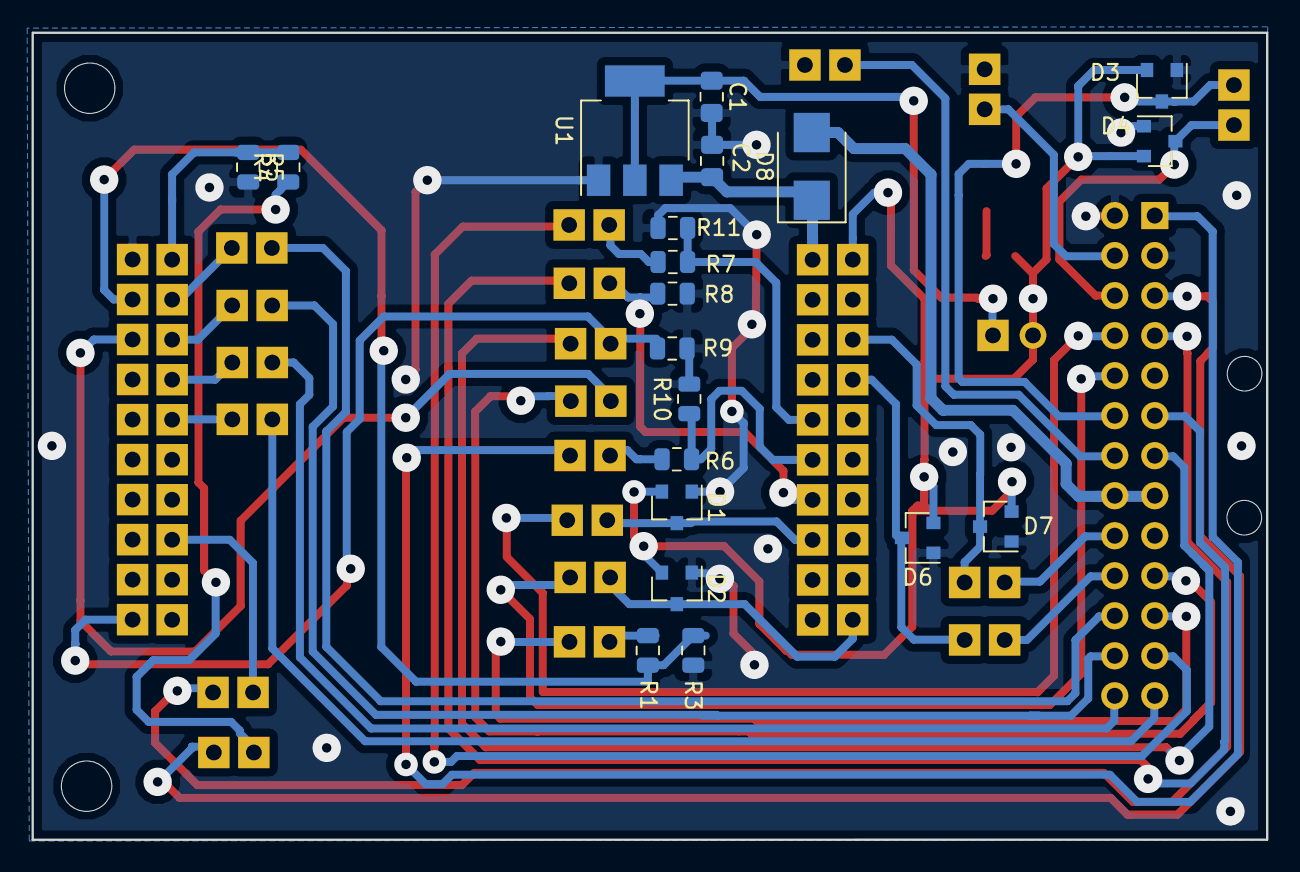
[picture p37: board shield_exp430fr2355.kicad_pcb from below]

Board: 2 copper layers, 78.4 x 51.2 mm, 51 parts (20 on the bottom side), 46 nets.

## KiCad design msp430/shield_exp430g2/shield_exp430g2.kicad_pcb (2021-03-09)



Board: 2 copper layers, 58.7 x 53.0 mm, 46 parts (20 on the bottom side), 46 nets.

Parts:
C1, C2: 100n; C_0805_2012Metric_Pad1.15x1.40mm_HandSolder
D1: LED; LED_0805_2012Metric
D2, D3, D4, D5, D6, D7: BAT54S; SOT-23
D8: D_Schottky; D_SMB
J1, J2: Digital; Socket_Strip_Arduino_1x10
J3, J4, J5, J6, J7, J8, J10, J11, J12, J13, J15, J16, J17, J18, J19, J20, J21, J22, J23, J24: Conn_01x02_Male; PinHeader_1x02_P2.54mm_Vertical
J9: Conn_02x13_Odd_Even; IDC-Header_2x13_P2.54mm_Vertical
J14: Conn_01x04_Male; PinHeader_1x04_P2.54mm_Vertical
R1: R; R_0805_2012Metric
R2, R4, R6, R7: 10k; R_0805_2012Metric
R3, R5, R8, R9, R10, R11: 15k; R_0805_2012Metric
U1: NCP1117-3.3_SOT223; SOT-223-3_TabPin2

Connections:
+3V3: D2.2, D3.2, D4.2, D5.2, D6.2, D7.2, J1.1, J3.2
+5V: C1.1, D8.1, J14.3, U1.3
+5VP: D8.2, J9.15, J9.16
ADC0: J6.1, J9.8
ADC1: J7.1, J9.10
ADC2: D4.3, J8.1, J9.12
ADC3: D5.3, J8.2, J9.6
AMP1: J4.1, J4.2, J9.4
AMP2: J5.2, J9.14
D0: J9.1, J21.1
D1: J9.23, J24.1
Echo0: J9.21, J10.1
Echo1: J9.5, J12.1
GND: C1.2, C2.2, D2.1, D3.1, D4.1, D5.1, D6.1, D7.1, J2.1, J5.1, J9.2, J9.3, J9.17, J14.4, R1.2, R3.2, R5.2, R8.2, R9.2, R10.2, R11.2, U1.1
L_TCRT: J9.13, J20.1
unnamed: C2.1, D1.2, J3.1, J14.1, J14.2, U1.2
unnamed: D1.1, R1.1
unnamed: J10.2, R2.1
unnamed: J12.2, R4.1
unnamed: J21.2, R6.1
unnamed: J24.2, R7.1
P1.0: D2.3, J1.2, J6.2
P1.1: D7.3, J1.3, J23.2
P1.2: D6.3, J1.4, J22.2
P1.3: D3.3, J1.5, J7.2
P1.4: J1.6, J11.2
P1.5: J1.7, R2.2, R3.1
P1.6: J2.7, R4.2, R5.1
P1.7: J2.6, J13.2
P2.0: J1.8, J19.2, R8.1
P2.1: J1.9, J15.2
P2.2: J1.10, J16.2
P2.3: J2.10, J20.2, R9.1
P2.4: J2.9, J17.2
P2.5: J2.8, J18.2
P2.6: J2.2, R6.2, R10.1
P2.7: J2.3, R7.2, R11.1
PWM1: J9.22, J15.1
PWM1N: J9.24, J16.1
PWM2: J9.26, J17.1
PWM2N: J9.25, J18.1
RXB: J9.20, J22.1
R_TCRT: J9.11, J19.1
TXB: J9.18, J23.1
Trig0: J9.19, J11.1
Trig1: J9.7, J13.1

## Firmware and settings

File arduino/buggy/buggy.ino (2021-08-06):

/*
  buggy.ino - Aplicação exemplo para o buggy 4x4
  
  - Exibe os dados dos sensores pelo terminal UART 9600 bps.
  - Recebe comandos da serial para movimentação dos motores.
  
  Created by Renan Augusto Starke, July 26, 2021.  
  Released into the public domain.
*/


#include "Motores.h"
#include "Ultrassom.h"
#include "Encoder.h"
#include "Baterias.h"
#include "Linha.h"

/* Tarefas básicas do exemplo */
void tarefa_1();
void tarefa_2();
volatile bool exibir_estado = true;

/* Instâncias das classe dos sensores/atuadores */
Motores motores;
Baterias baterias;
Linha seguidor_linha;
Ultrassom ultrassom_1(Ultrassom::ECHO1, Ultrassom::TRIG1);
Encoder encoder_0 (Encoder::D0);


/* Configuração e mensagem inicial */
void setup() {
  
  Serial.begin(9600);
  while (!Serial); 

  Serial.println("Teste buggy 4x4");
  Serial.println("f: mover para frente");
  Serial.println("r: mover para trás");
  Serial.println("e: mover para esquerda");
  Serial.println("d: mover para direita");  
  Serial.println("s: exibir estado dos sensores a cada 1s");
  Serial.println("i: exibir descrição das dos estados");

  delay(5000);  

}

/* Loop de atualização do sensores e das tarefas */
void loop() {
  
  encoder_0.atualizar();
  ultrassom_1.atualizar();

 
  tarefa_1();
  tarefa_2();
}

/* Tarefa 2: comandos da serial */
void tarefa_1(){

  /* Caso tenha recebido algum dado do PC */
  if (Serial.available()) {
     char dado_recebido = Serial.read();
     
      if (dado_recebido == 'p')
          motores.parar();          
      else if (dado_recebido == 'f')
          motores.frente(200);      
      else if (dado_recebido == 'r')
          motores.tras(200);      
      else if (dado_recebido == 'e')
          motores.esquerda(150);          
      else if (dado_recebido == 'd')
          motores.direita(150);
      else if (dado_recebido == 's') {
        if (exibir_estado == true)
          exibir_estado = false;
        else
          exibir_estado = true;        
      }
      
      if (dado_recebido == 'i') {
        Serial.println("Bat0\tBat1\tVelocidade\tDistância");
      }

  }
}

/* Exibe dados dos sensores */
void tarefa_2(){
  static unsigned long tempo_atual = 0;

  /* Escalonamento a cada 1s. Se ativado a exibição */
  if ((exibir_estado) && (millis() - tempo_atual >= 1000)){
    
    Serial.print(baterias.obter_bateria_0());
    Serial.print("\t");
    Serial.print(baterias.obter_bateria_1());
    Serial.print("\t");
    Serial.print(encoder_0.obter_velocidade());
    Serial.print("\t");
    Serial.print(ultrassom_1.obter_distancia());
    Serial.print("\t");
    Serial.print(seguidor_linha.obter_esquerda());
    Serial.print("\t");
    Serial.print(seguidor_linha.obter_direita());
    
    Serial.println("");
    
    tempo_atual = millis();    
  }  
}

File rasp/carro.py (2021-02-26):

# Copyright (c) 2020 Instituto Federal de Santa Catarina
# Author: Renan Augusto Starke
#
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
import pigpio
import time
import motor
import bateria
import encoder
import sensor_linha
import ultrassom

import threading, time
from datetime import timedelta


def mostrar_sensores(ultrassom, encoder, esquerda, direita, baterias, stop):
    
    while (stop() != True):    
        distancia = ultrassom.obter()
        velocidade = encoder.obter()
        linha_e = esquerda.obter()
        linha_d = direita.obter()
        bat_1 = baterias.obter(1)
        bat_2 = baterias.obter(2)
        
        print("{:>5.3f}\t{:>5.3f}\t{:>d}\t{:>d}\t{:>5.3f}\t{:>5.3f}".format(distancia, velocidade, linha_e, linha_d, bat_1, bat_2))
              
        time.sleep(1)
   
    
def main():
    print('Hello!')
    print('Digite a direção: ')
    print('p: parar')
    print('r: ré')
    print('e: esquerda')
    print('p: direita')
    print('q: sair')
        
    pinos = pigpio.pi()
    
    encoder_1 = encoder.Encoder(pinos,5)
    encoder_1.iniciar()
    
    ultrassom_1 = ultrassom.Ultrassom(pinos, 24, 22)
    ultrassom_1.iniciar()
    
    esquerda = sensor_linha.Sensor_linha(pinos, 8)
    direita = sensor_linha.Sensor_linha(pinos, 7)
    
    motores = motor.Motor(pinos)
    baterias = bateria.Bateria(pinos)
    baterias.iniciar()
    
    stop = False
    sensores_debug = threading.Thread(target=mostrar_sensores, args=(ultrassom_1, encoder_1, esquerda, direita, baterias, lambda: stop));       
    sensores_debug.start()
    
    dir = 's'
    
    # motores.mover_frente(100)
    
    while (dir != 'q'):
        
        dir = input()
        
        if dir == 'p':
            motores.parar()
            
        if dir == 'f':
            motores.mover_frente(100)
        
        if dir == 'r':
            motores.mover_re(40)
        
        if dir == 'e':
            motores.mover_esquerda(75)
            
        if dir == 'd':
            motores.mover_direita(75)
            
        # print("{:>5.3f}\t{:>5.3f}".format(baterias.bateria_1, baterias.bateria_2))
        
        time.sleep(1)        
        
        
    baterias.parar()
    motores.parar()
    encoder_1.parar()
    esquerda.parar()
    direita.parar()
    ultrassom_1.parar()
    
    stop = True
    sensores_debug.join()
    
    print('Bye Bye!')    

if __name__ == '__main__':
    main()

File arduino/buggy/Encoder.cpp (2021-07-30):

/*
  Encoder.cpp - Biblioteca para mediação de velocidade usando encoder para buggy 4x4.
  Created by Renan Augusto Starke, July 26, 2021.
  Released into the public domain.
*/

#include "Encoder.h"

/* Cabeçalhos e vetores de interrupções: código low level para PCINTs */
#include <avr/io.h>
#include <avr/interrupt.h>

volatile unsigned long Encoder::pulsos_d0 = 0;
volatile unsigned long Encoder::pulsos_d1 = 0;

Encoder::Encoder(unsigned char pino)
{
  /* Configuração dos pinos */
  pinMode(pino, INPUT);

  tempo = 0;
  
  /* Guarda informaçẽos dos pinos */
  _pino = pino;
  
  /* Contagem dos pulsos */  
  pulsos_d0 = 0;
  pulsos_d1 = 0;

  /* attachInterrupt: implementado apenas para IRQ externa 0 e 1 
   * attachInterrupt(pino, Encoder::contador, FALLING);  
   *
   *  Pinos D0 e D1 estão mapeados em PCINT4(PB4) e PCINT5 (PB5)   */
  if (pino == Encoder::D0)
    PCMSK0 |= (1 << PCINT5);
  else
    PCMSK0 |= (1 << PCINT4);
   
  PCICR |= 1 << PCIE0;  
}

/* PCINT deve-se testar qual pino gerou a IRQ */
ISR(PCINT0_vect)
{
  /* Teste para D0 */
  if (PINB & (1 << PB5)){
    Encoder::pulsos_d0++;    
  }

  /* Teste para D1 */
  if (PINB & (1 << PB4))
    Encoder::pulsos_d1++;



}

void Encoder::atualizar(){
  unsigned long pulsos = 0;
  
  /* Mede a velocidade a cada 500 ms */
  if (millis() - tempo >= 500)
  {
    /* Desabilita interrupcao durante o calculo */       
    if (_pino == Encoder::D0){
      /* Desabilita interrupcao durante o calculo */
      PCMSK0 &= ~(1 << PCINT5);
      pulsos = pulsos_d0;
      pulsos_d0 = 0;
    }
    else {
      PCMSK0 &= ~(1 << PCINT4);
      pulsos = pulsos_d1;
      pulsos_d1 = 0;
    }
      
    /* velocidade = (60 * 1000 / pulsos_por_volta ) / (millis() - tempo) * pulsos; */
    velocidade = pulsos << 2;          //Rever: usar 500ms para multipliar por 2
    tempo = millis();

    if (_pino == Encoder::D0)
      PCMSK0 |= (1 << PCINT5);
    else
      PCMSK0 |= (1 << PCINT4);    
  }  
}

unsigned long Encoder::obter_velocidade(){
  return velocidade;
}

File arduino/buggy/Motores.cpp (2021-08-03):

/*
  Motores.cpp - Biblioteca para controle de motores do Buggy 4x4.
  Created by Renan Augusto Starke, July 22, 2021.
  Released into the public domain.
*/

#include "Motores.h"

Motores::Motores()
{
  /* Configuração dos pinos */
  pinMode(M1, OUTPUT);
  pinMode(M1N, OUTPUT);
  pinMode(M2, OUTPUT);
  pinMode(M2N, OUTPUT);
}

void Motores::parar()
{
  /* Desliga todos os motores */
  digitalWrite(M1, LOW);
  digitalWrite(M1N, LOW);
  digitalWrite(M2, LOW);
  digitalWrite(M2N, LOW);  
}


void Motores::frente(unsigned char velocidade){
  parar();

  /*digitalWrite(M1, HIGH);  
  digitalWrite(M2, HIGH); */
  velocidade &= 0xff;

  analogWrite(M1, velocidade);
  analogWrite(M2, velocidade);

}

void Motores::tras(unsigned char velocidade){
  parar();

  velocidade &= 0xff;
  /* digitalWrite(M1N, HIGH);
  digitalWrite(M2N, HIGH); */

  analogWrite(M1N, velocidade);
  analogWrite(M2N, velocidade);

}

void Motores::direita(unsigned char velocidade){
  parar();
  velocidade &= 0xff;
  
  /*digitalWrite(M1, HIGH);
  digitalWrite(M2N, HIGH);*/

  analogWrite(M1, velocidade);
  analogWrite(M2N, velocidade);

  
}

void Motores::esquerda(unsigned char velocidade){
  parar();
  velocidade &= 0xff;

  /* digitalWrite(M2N, HIGH);
  digitalWrite(M1, HIGH);  */

  analogWrite(M2, velocidade);
  analogWrite(M1N, velocidade);
}

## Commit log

2020-06-29 First commit, added PWM examples
2020-09-21 Added hardware files
    [hardware.kicad_pcb, hardware.sch]
2020-09-24 Added silk labels
    [hardware.kicad_pcb]
2020-10-22 Added diode
    [hardware.kicad_pcb, hardware.sch]
2020-11-11 Added aligment holes
    [hardware.kicad_pcb]
2020-12-14 Added i2c connector
    [hardware.kicad_pcb, hardware.sch]
2020-12-15 Change 26vias connector
    [hardware.kicad_pcb, hardware.sch]
2020-12-15 Added motor class
    [hardware.sch]
2021-02-09 Added threads, first enconder test
2021-02-09 Added encoder file
2021-02-10 Change encoder gpio library
    [hardware.sch]
2021-02-12 Added line sensor
2021-02-12 Added line sensor, with file
2021-02-26 Added thread for debuging
2021-03-09 Added boards
    [3dmodel.FCStd, Hardware-backup.kicad_pcb, Hardware.kicad_pcb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]
2021-07-20 Added ultrassonic sensor mounts
2021-07-22 Added arduino motor class
    [hardware.kicad_pcb]
2021-07-27 Added encoder pcints
2021-07-30 Implemented battery class
    [Hardware.sch]
2021-08-03 Corrigido bug nos motores, implementado app principal
    [Motores.cpp, Ultrassom.cpp, buggy.ino]
2021-08-03 Adicionado sensor de linha
2021-08-06 Adicionado sensor de linha nos estados
2022-06-03 Atualizado pdf do esquemático
    [shield_exp430fr2355.kicad_sch]
2022-07-05 Update schemetic
    [shield_exp430fr2355.kicad_sch]
2022-09-08 Atualizado esquematico pdf
    [veiculo_uno.kicad_sch]
